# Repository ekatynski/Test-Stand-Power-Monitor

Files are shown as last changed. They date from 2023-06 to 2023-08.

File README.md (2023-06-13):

View this project on [CADLAB.io](https://cadlab.io/project/27045). 

# Test-Stand-Power-Monitor
A small board for cheaply and easily monitoring a motor test stand for a host of data types.

## Function
This board is capable of monitoring the following:
- 1x Voltage input
- 1x Hall Effect Sensor output (current measuring)
- 1x Displacement Sensor interface
- 1x UART (ESCs have UART telemetry output)
- 1x 1K RTD for temperature monitoring

In addition, this board is capable of operating a relay to control a contactor protecting the test stand power supply, as well as a CAN bus to interface with other sensory hardware in development utilizing CAN. In doing so, this board could monitor ESC power consumption, ESC temperature, ESC telemetry output, motor displacement, and eventually eRPM pending future hardware development. Prior test stand setups had used a Teensy 4.1 to monitor telemetry and perform no other function, so this board's development was to expand the amount of test stand monitoring that could be done cheaply while using a less costly and more available microcontroller in the event that it were damaged and required replacement.

## To-Do
Firmware to perform said monitoring has not yet been developed. This board utilizes an ESP32 microcontroller, chosen because it can be configured to communicate over WiFi out of the box, but I have not taken the time to write the C++ needed to make this board useful yet.

## Assembly Guide
If interested, an interactive BOM is available in this repo at `/bom/Test-Stand-Power-Monitor_2023-06-12_22-39-21.html`.

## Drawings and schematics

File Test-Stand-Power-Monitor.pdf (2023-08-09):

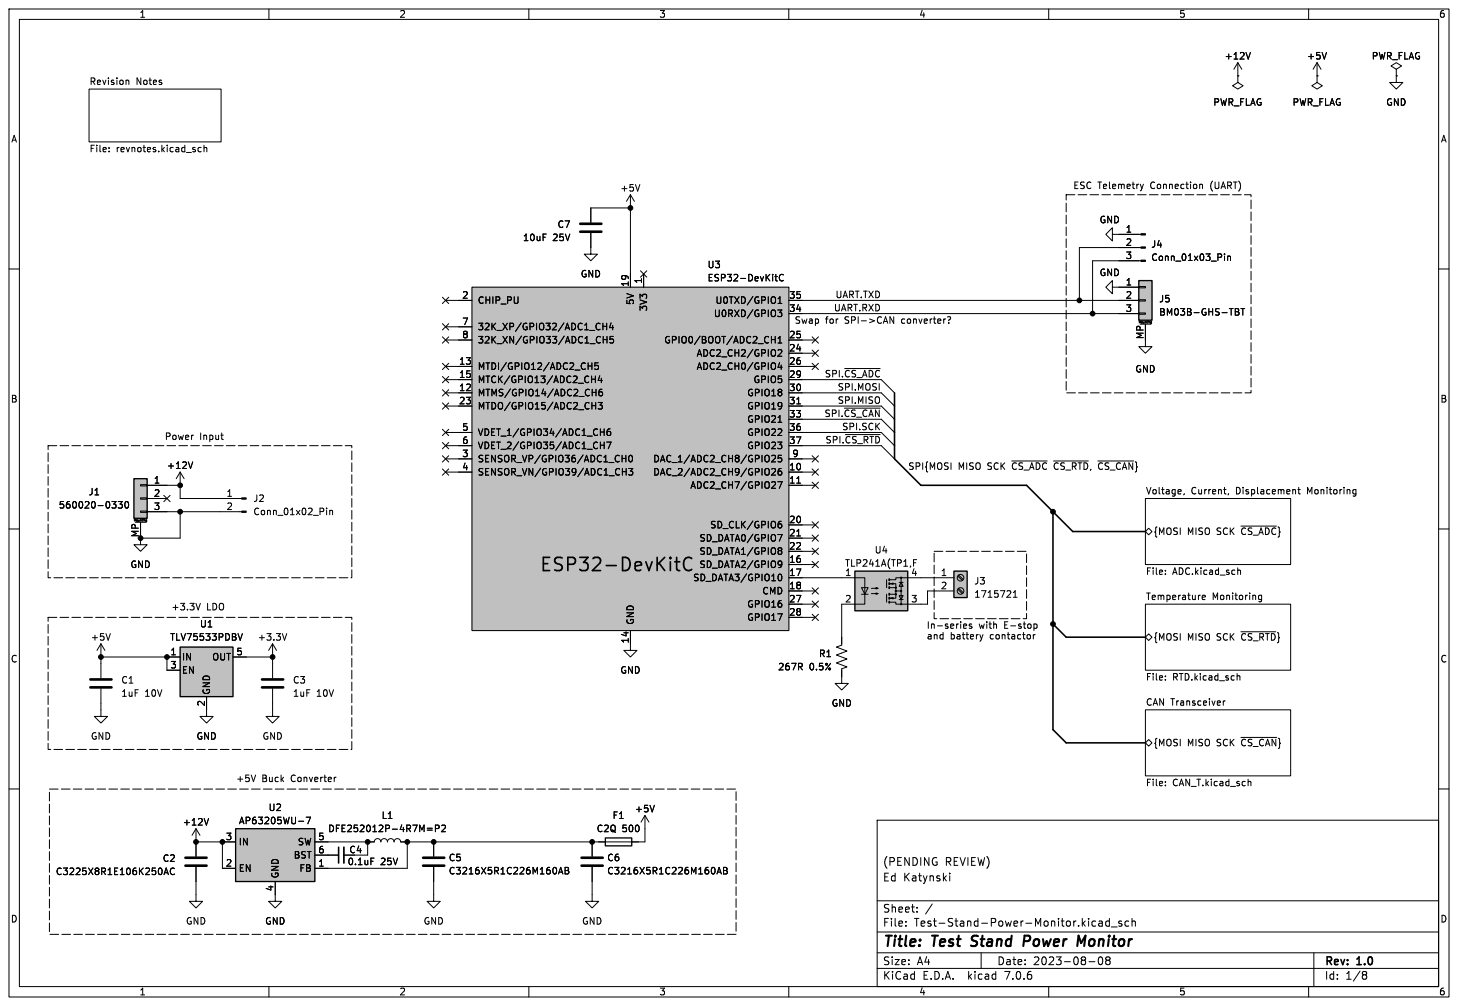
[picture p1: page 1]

Revision Notes File: revnotes.kicad_sch

1 DAC_2/ADC2_CH9/GPIO26 10 ADC2_CH7/GPIO27 11 MTMS/GPIO14/ADC2_CH6 12 MTDI/GPIO12/ADC2_CH5 13 MTCK/GPIO13/ADC2_CH4 15 SD_DATA2/GPIO9 16 SD_DATA3/GPIO10 17 CMD 18 CHIP_PU 2 SD_CLK/GPIO6 20 SD_DATA0/GPIO7 21 SD_DATA1/GPIO8 22 MTDO/GPIO15/ADC2_CH3 23 ADC2_CH2/GPIO2 24 GPIO0/BOOT/ADC2_CH1 25 ADC2_CH0/GPIO4 26 GPIO16 27 GPIO17 28 GPIO5 29 SENSOR_VP/GPIO36/ADC1_CH0 3 GPIO18 30 GPIO19 31 GPIO21 33 U0RXD/GPIO3 34 U0TXD/GPIO1 35 GPIO22 36 GPIO23 37 SENSOR_VN/GPIO39/ADC1_CH3 4 VDET_1/GPIO34/ADC1_CH6 5 VDET_2/GPIO35/ADC1_CH7 6

SPI{MOSI MISO SCK ~{CS_ADC}~{CS_RTD},~{CS_CAN}} SPI.MOSI
SPI.MISO
SPI.~{CS_CAN} SPI.SCK

{MOSI MISO SCK ~{CS_CAN}} CAN Transceiver File: CAN_T.kicad_sch

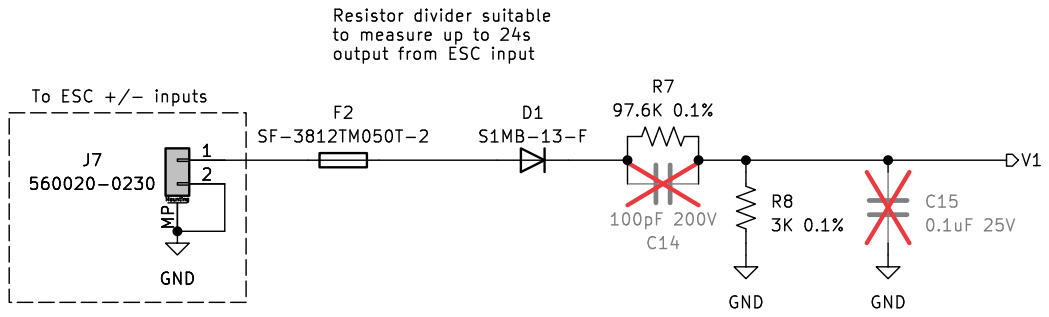
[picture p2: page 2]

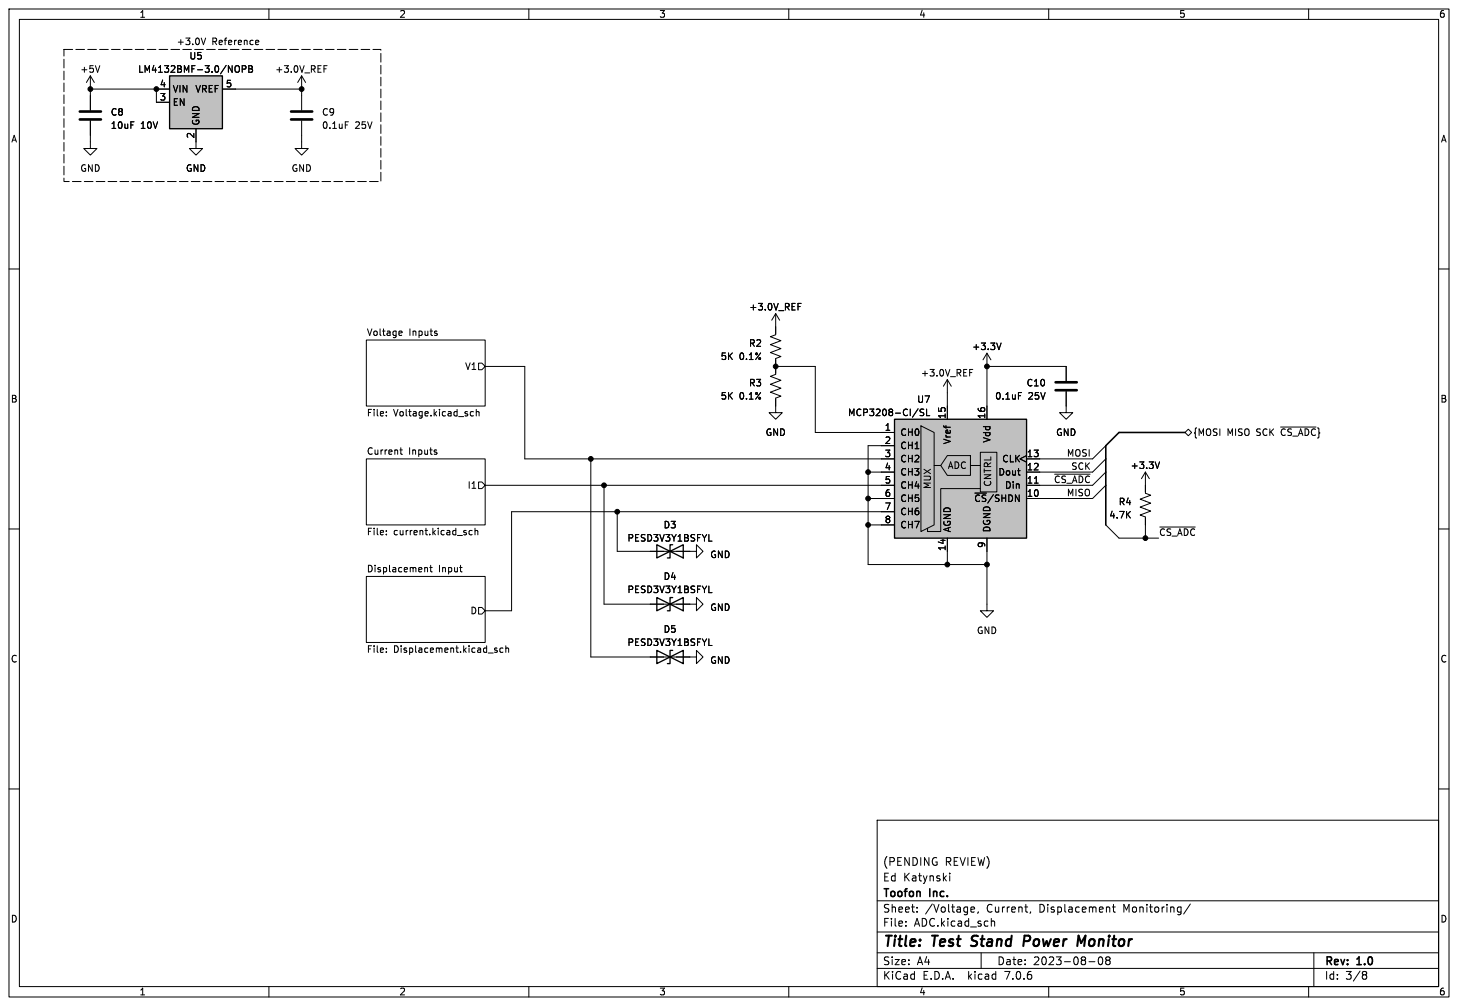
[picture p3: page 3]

V1 Voltage Inputs File: Voltage.kicad_sch D

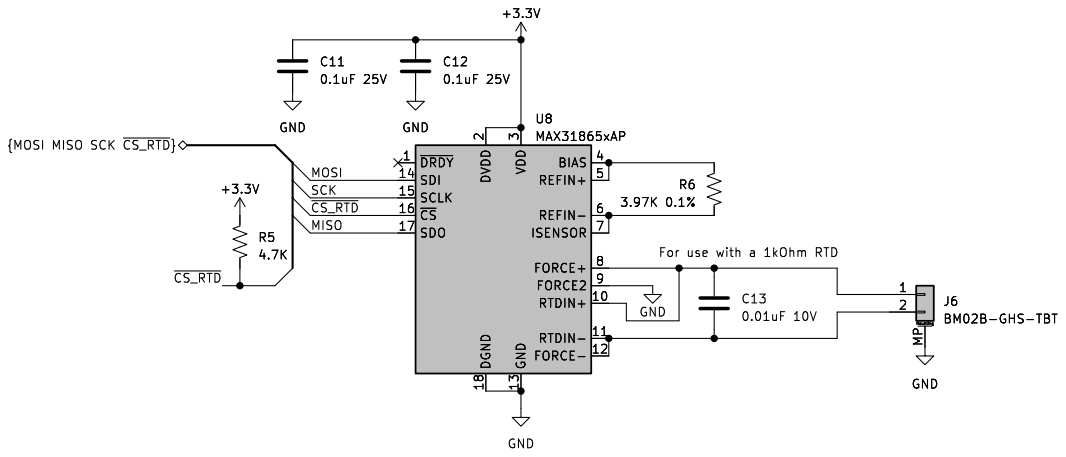
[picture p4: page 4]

J6BM02B-GHS-TBT GND GND

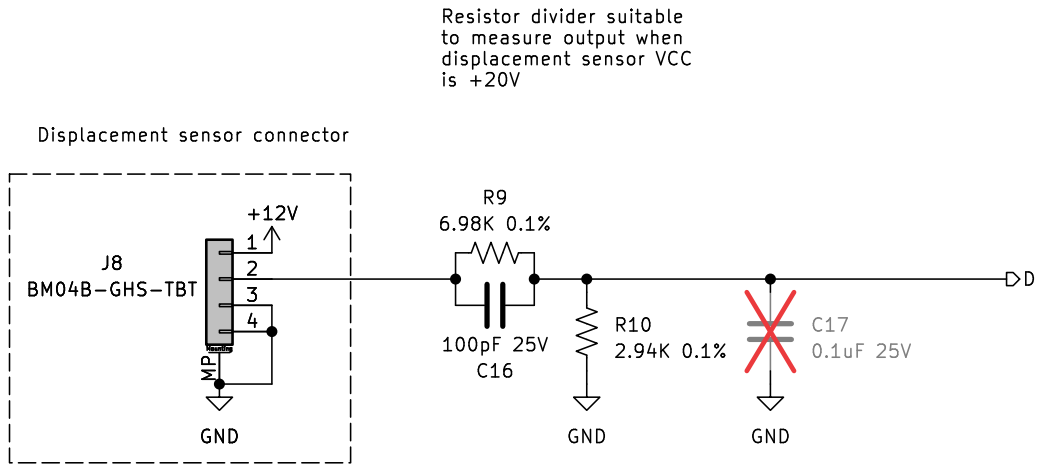
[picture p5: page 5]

to measure output when

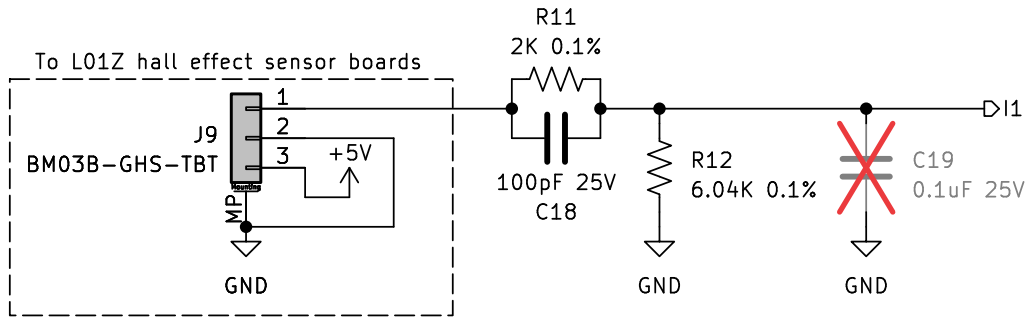
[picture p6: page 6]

I1 To L01Z hall effect sensor boards GND

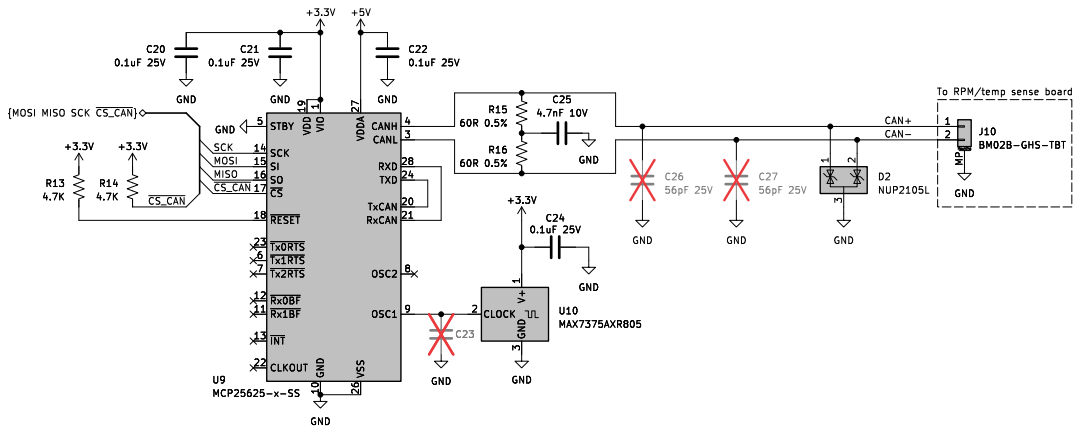
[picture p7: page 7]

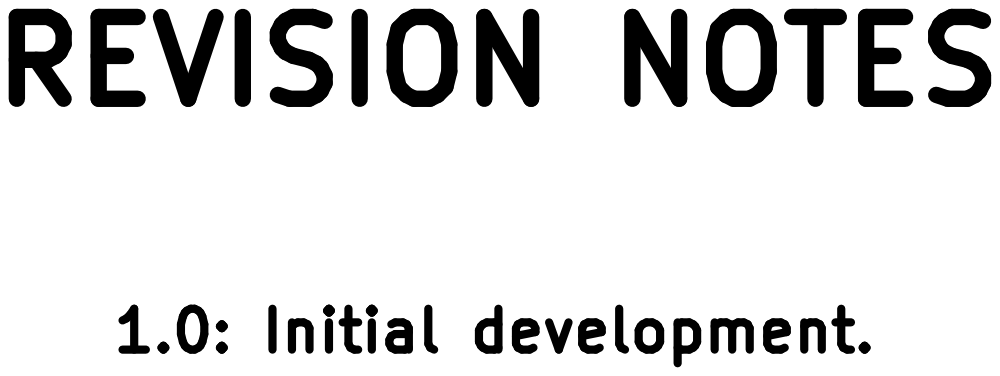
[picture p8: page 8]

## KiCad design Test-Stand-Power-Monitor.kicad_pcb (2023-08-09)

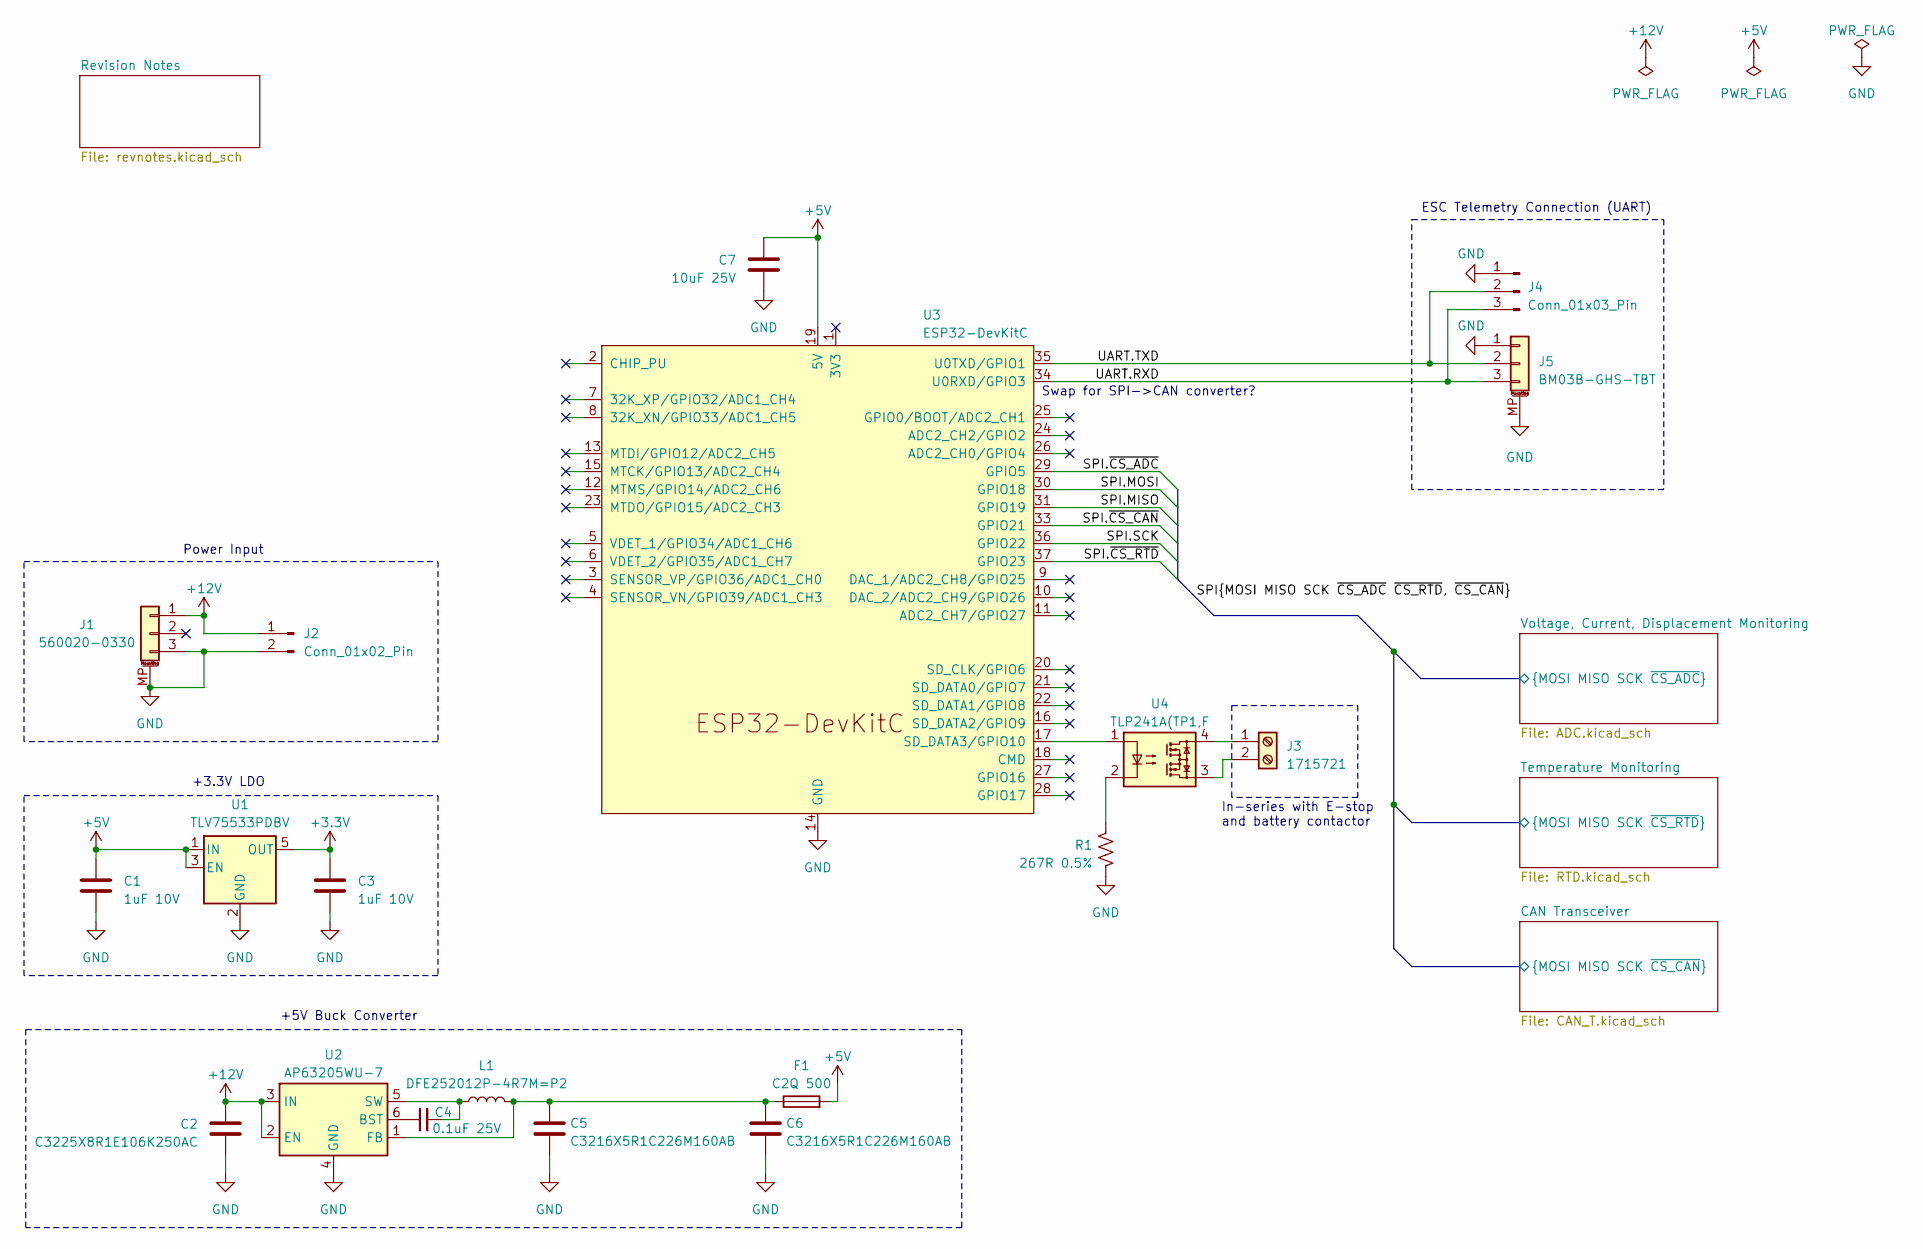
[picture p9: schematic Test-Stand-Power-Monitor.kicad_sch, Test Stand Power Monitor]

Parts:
C1, C3: 1uF 10V; C_0603_1608Metric_Pad1.08x0.95mm_HandSolder
C2: C3225X8R1E106K250AC; C_1210_3225Metric
C4: 0.1uF 25V; C_0402_1005Metric_Pad0.74x0.62mm_HandSolder
C5, C6: C3216X5R1C226M160AB; C_1206_3216Metric
C7: 10uF 25V; C_0603_1608Metric_Pad1.08x0.95mm_HandSolder
F1: C2Q 500; Fuse_0603_1608Metric
J1: 560020-0330; MOLEX_5600200330
J2: Conn_01x02_Pin; PinHeader_1x02_P2.54mm_Vertical
J3: 1715721; TerminalBlock_Phoenix_MKDS-1,5-2-5.08_1x02_P5.08mm_Horizont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
J4: Conn_01x03_Pin; PinHeader_1x03_P2.54mm_Vertical
J5: BM03B-GHS-TBT; JST_GH_BM03B-GHS-TBT_1x03-1MP_P1.25mm_Vertical
L1: DFE252012P-4R7M=P2; L_1008_2520Metric_Pad1.43x2.20mm_HandSolder
R1: 267R 0.5%; R_0402_1005Metric_Pad0.72x0.64mm_HandSolder
U1: TLV75533PDBV; SOT-23-5
U2: AP63205WU-7; TSOT-23-6
U3: ESP32-DevKitC
U4: TLP241A(TP1,F; OnSemi_CASE100CY

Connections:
+3.3V: C3.1, U1.5 (OUT); also elsewhere on the board
+5V: C1.1, C7.1, F1.2, U1.1 (IN), U1.3 (EN), U3.19 (5V); also elsewhere on the board
+12V: C2.1, J1.1, J2.1, U2.2 (EN), U2.3 (IN); also elsewhere on the board
/SPI.MISO: U3.31 (GPIO19); also elsewhere on the board
/SPI.MOSI: U3.30 (GPIO18); also elsewhere on the board
/SPI.SCK: U3.36 (GPIO22); also elsewhere on the board
/SPI.~CS_ADC: U3.29 (GPIO5); also elsewhere on the board
/SPI.~CS_CAN: U3.33 (GPIO21); also elsewhere on the board
/SPI.~CS_RTD: U3.37 (GPIO23); also elsewhere on the board
/UART.RXD: J4.3, J5.3, U3.34 (U0RXD/GPIO3)
/UART.TXD: J4.2, J5.2, U3.35 (U0TXD/GPIO1)
GND: C1.2, C2.2, C3.2, C5.2, C6.2, C7.2, J1.3, J1.MP (MountPin), J2.2, J4.1, J5.1, J5.MP (MountPin), R1.2, U1.2 (GND), U2.4 (GND), U3.14 (GND), U3.32 (GND), U3.38 (GND); also elsewhere on the board
unnamed: J3.1, U4.4
unnamed: J3.2, U4.3
unnamed: R1.1, U4.2
unnamed: C4.1, U2.6 (BST)
unnamed: C5.1, C6.1, F1.1, L1.2, U2.1 (FB)
unnamed: C4.2, L1.1, U2.5 (SW)
unnamed: U3.17 (SD_DATA3/GPIO10), U4.1

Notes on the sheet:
In-series with E-stop and battery contactor
Power Input
+3.3V LDO
ESC Telemetry Connection (UART)
+5V Buck Converter
Swap for SPI->CAN converter?

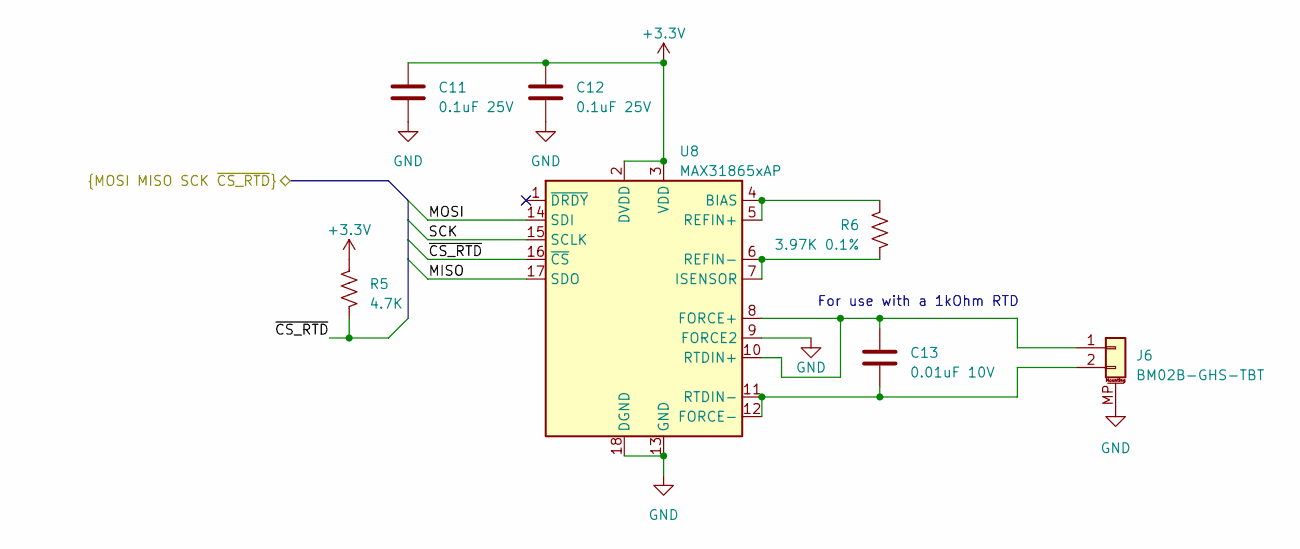
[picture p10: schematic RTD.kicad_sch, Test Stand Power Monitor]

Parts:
C11, C12: 0.1uF 25V; C_0402_1005Metric_Pad0.74x0.62mm_HandSolder
C13: 0.01uF 10V; C_0402_1005Metric_Pad0.74x0.62mm_HandSolder
J6: BM02B-GHS-TBT; JST_GH_BM02B-GHS-TBT_1x02-1MP_P1.25mm_Vertical
R5: 4.7K; R_0402_1005Metric_Pad0.72x0.64mm_HandSolder
R6: 3.97K 0.1%; R_0402_1005Metric_Pad0.72x0.64mm_HandSolder
U8: MAX31865xAP; SSOP-20_5.3x7.2mm_P0.65mm

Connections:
+3.3V: C11.1, C12.1, R5.1, U8.2 (DVDD), U8.3 (VDD); also elsewhere on the board
/SPI.MISO: U8.17 (SDO); also elsewhere on the board
/SPI.MOSI: U8.14 (SDI); also elsewhere on the board
/SPI.SCK: U8.15 (SCLK); also elsewhere on the board
/SPI.~CS_RTD: R5.2, U8.16 (~CS); also elsewhere on the board
GND: C11.2, C12.2, J6.MP (MountPin), U8.9 (FORCE2), U8.13 (GND), U8.18 (DGND), U8.19 (GND); also elsewhere on the board
unnamed: C13.1, J6.1, U8.8 (FORCE+), U8.10 (RTDIN+)
unnamed: C13.2, J6.2, U8.11 (RTDIN-), U8.12 (FORCE-)
unnamed: R6.1, U8.4 (BIAS), U8.5 (REFIN+)
unnamed: R6.2, U8.6 (REFIN-), U8.7 (ISENSOR)

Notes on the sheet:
For use with a 1kOhm RTD

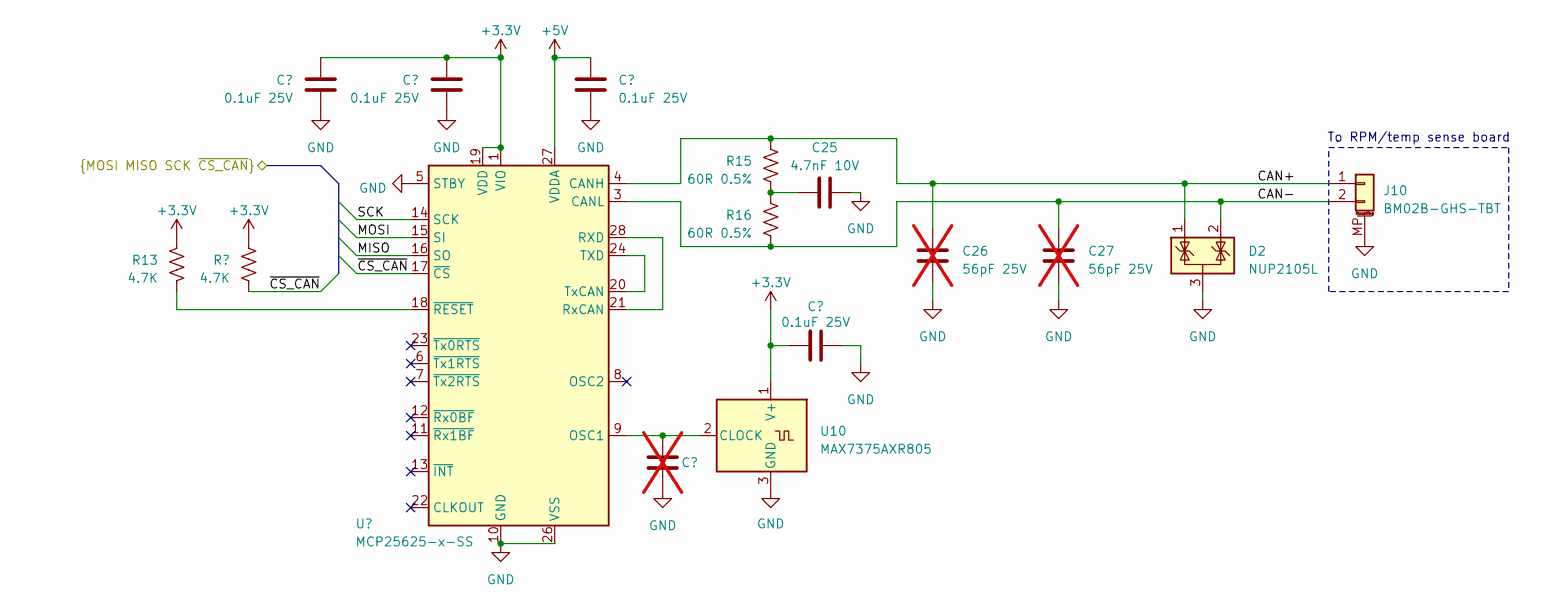
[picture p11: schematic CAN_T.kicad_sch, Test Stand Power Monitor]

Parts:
C20, C21, C22, C24: 0.1uF 25V; C_0402_1005Metric_Pad0.74x0.62mm_HandSolder
C23: C_0402_1005Metric_Pad0.74x0.62mm_HandSolder; not fitted
C25: 4.7nF 10V; C_0402_1005Metric_Pad0.74x0.62mm_HandSolder
C26, C27: 56pF 25V; C_0402_1005Metric_Pad0.74x0.62mm_HandSolder; not fitted
D2: NUP2105L; SOT-23
J10: BM02B-GHS-TBT; JST_GH_BM02B-GHS-TBT_1x02-1MP_P1.25mm_Vertical
R13, R14: 4.7K; R_0402_1005Metric_Pad0.72x0.64mm_HandSolder
R15, R16: 60R 0.5%; R_0603_1608Metric_Pad0.98x0.95mm_HandSolder
U9: MCP25625-x-SS; SSOP-28_5.3x10.2mm_P0.65mm
U10: MAX7375AXR805; SOT-323_SC-70

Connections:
+3.3V: C20.1, C21.1, C24.1, R13.1, R14.1, U9.1 (VIO), U9.19 (VDD), U10.1 (V+); also elsewhere on the board
+5V: C22.1, U9.27 (VDDA); also elsewhere on the board
/CAN Transceiver/CAN+: C26.2, D2.1 (K), J10.1, R15.1, U9.4 (CANH)
/CAN Transceiver/CAN-: C27.2, D2.2 (K), J10.2, R16.2, U9.3 (CANL)
/SPI.MISO: U9.16 (SO); also elsewhere on the board
/SPI.MOSI: U9.15 (SI); also elsewhere on the board
/SPI.SCK: U9.14 (SCK); also elsewhere on the board
/SPI.~CS_CAN: R14.2, U9.17 (~CS); also elsewhere on the board
GND: C20.2, C21.2, C22.2, C23.2, C24.2, C25.2, C26.1, C27.1, D2.3 (A), J10.MP (MountPin), U9.5 (STBY), U9.10 (GND), U9.26 (VSS), U10.3 (GND); also elsewhere on the board
unnamed: C25.1, R15.2, R16.1
unnamed: U9.21 (RxCAN), U9.28 (RXD)
unnamed: U9.20 (TxCAN), U9.24 (TXD)
unnamed: R13.2, U9.18 (~RESET)
unnamed: C23.1, U9.9 (OSC1), U10.2 (CLOCK)

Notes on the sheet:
To RPM/temp sense board

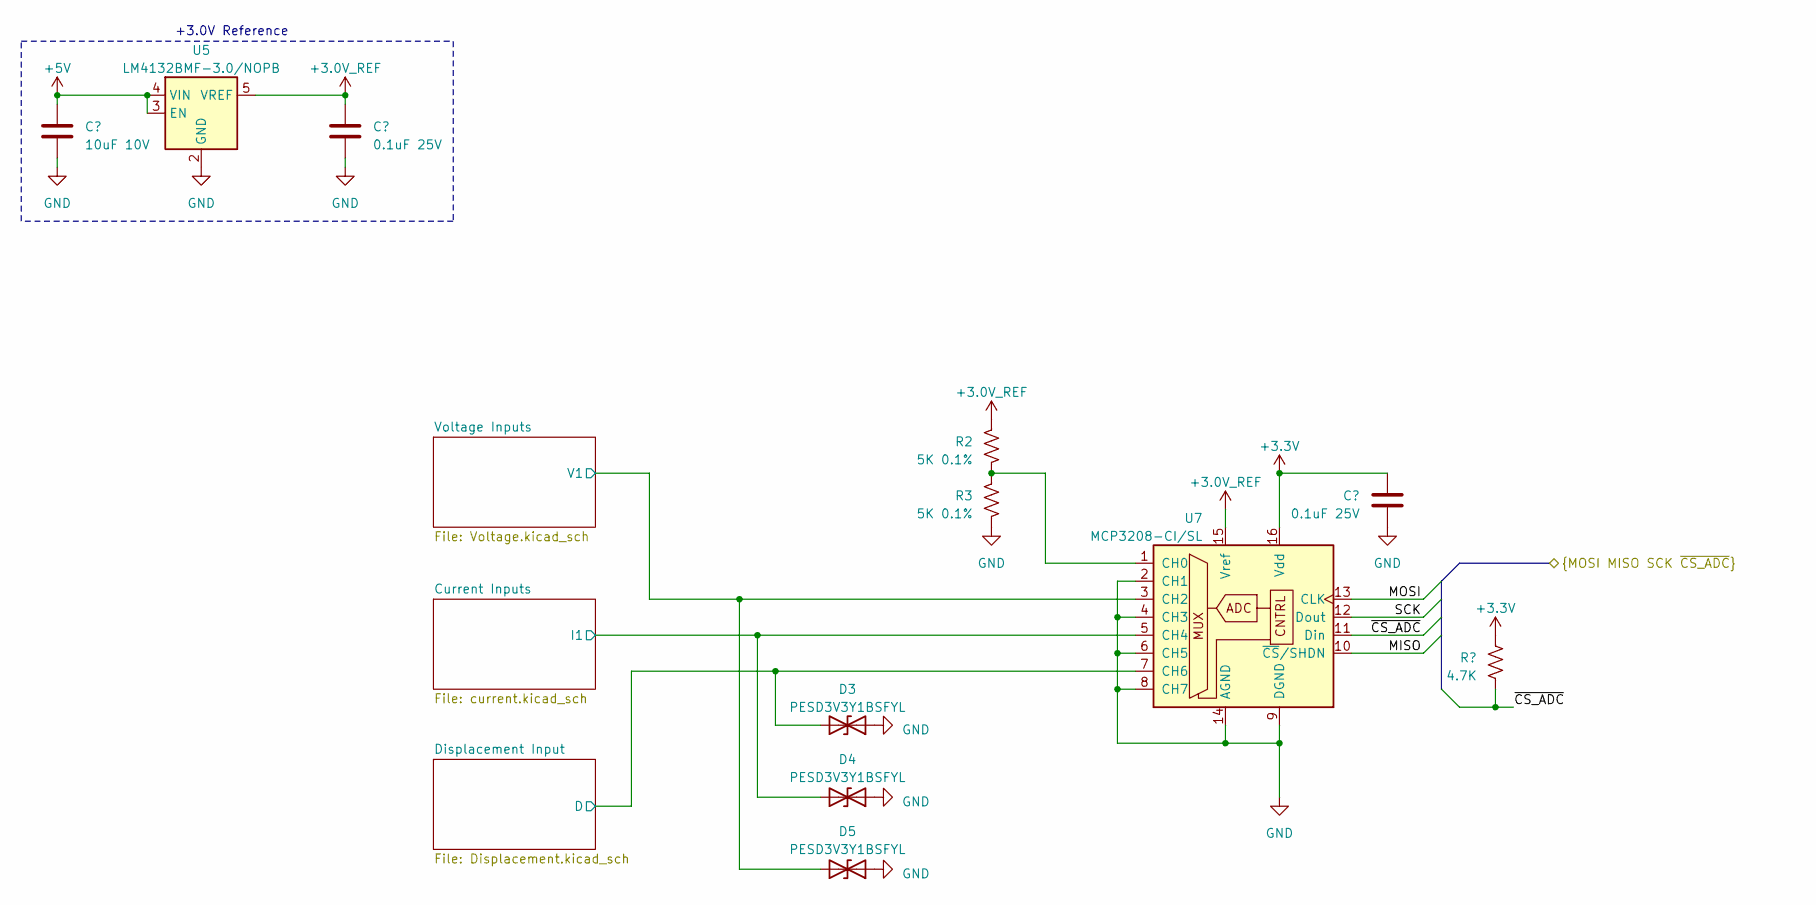
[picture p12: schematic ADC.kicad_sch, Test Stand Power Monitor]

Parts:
C8: 10uF 10V; C_0603_1608Metric_Pad1.08x0.95mm_HandSolder
C9, C10: 0.1uF 25V; C_0402_1005Metric_Pad0.74x0.62mm_HandSolder
D3, D4, D5: PESD3V3Y1BSFYL; D_0201_0603Metric
R2, R3: 5K 0.1%; R_0402_1005Metric_Pad0.72x0.64mm_HandSolder
R4: 4.7K; R_0402_1005Metric_Pad0.72x0.64mm_HandSolder
U5: LM4132BMF-3.0/NOPB; SOT-23-5
U7: MCP3208-CI/SL; SOIC-16_3.9x9.9mm_P1.27mm

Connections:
+3.0V_REF: C9.1, R2.1, U5.5 (VREF), U7.15 (Vref)
+3.3V: C10.1, R4.1, U7.16 (Vdd); also elsewhere on the board
+5V: C8.1, U5.3 (EN), U5.4 (VIN); also elsewhere on the board
/SPI.MISO: U7.10 (~CS/SHDN); also elsewhere on the board
/SPI.MOSI: U7.13 (CLK); also elsewhere on the board
/SPI.SCK: U7.12 (Dout); also elsewhere on the board
/SPI.~CS_ADC: R4.2, U7.11 (Din); also elsewhere on the board
/Voltage, Current, Displacement Monitoring/Current Inputs/I1: D4.2 (A2), U7.5 (CH4); also elsewhere on the board
/Voltage, Current, Displacement Monitoring/Displacement Input/D: D3.2 (A2), U7.7 (CH6); also elsewhere on the board
/Voltage, Current, Displacement Monitoring/Voltage Inputs/V1: D5.2 (A2), U7.3 (CH2); also elsewhere on the board
GND: C8.2, C9.2, C10.2, D3.1 (A1), D4.1 (A1), D5.1 (A1), R3.2, U5.2 (GND), U7.2 (CH1), U7.4 (CH3), U7.6 (CH5), U7.8 (CH7), U7.9 (DGND), U7.14 (AGND); also elsewhere on the board
unnamed: R2.2, R3.1, U7.1 (CH0)

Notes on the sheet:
+3.0V Reference

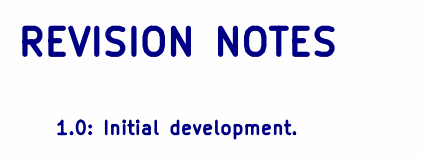
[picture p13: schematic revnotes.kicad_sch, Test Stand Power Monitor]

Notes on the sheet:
REVISION NOTES
1.0: Initial development.

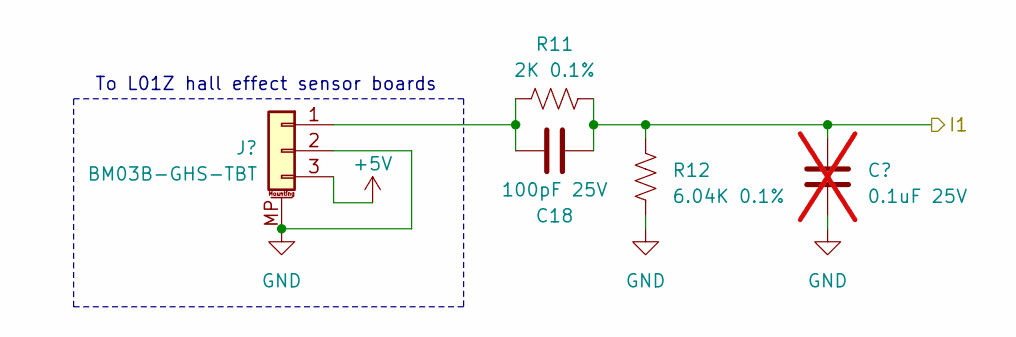
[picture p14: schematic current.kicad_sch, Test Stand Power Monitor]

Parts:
C18: 100pF 25V; C_0402_1005Metric_Pad0.74x0.62mm_HandSolder
C19: 0.1uF 25V; C_0402_1005Metric_Pad0.74x0.62mm_HandSolder; not fitted
J9: BM03B-GHS-TBT; JST_GH_BM03B-GHS-TBT_1x03-1MP_P1.25mm_Vertical
R11: 2K 0.1%; R_0402_1005Metric_Pad0.72x0.64mm_HandSolder
R12: 6.04K 0.1%; R_0402_1005Metric_Pad0.72x0.64mm_HandSolder

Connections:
+5V: J9.3; also elsewhere on the board
/Voltage, Current, Displacement Monitoring/Current Inputs/I1: C18.2, C19.1, R11.2, R12.1; also elsewhere on the board
GND: C19.2, J9.2, J9.MP (MountPin), R12.2; also elsewhere on the board
unnamed: C18.1, J9.1, R11.1

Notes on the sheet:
To L01Z hall effect sensor boards

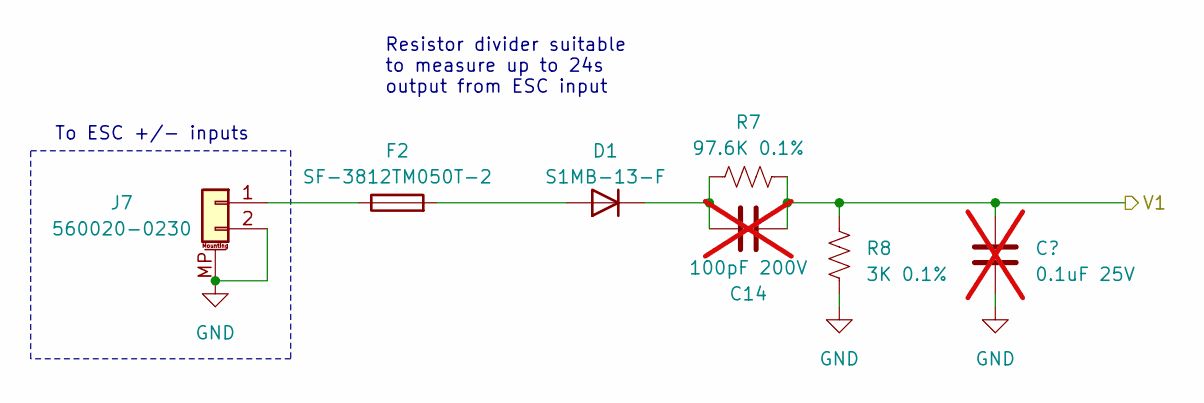
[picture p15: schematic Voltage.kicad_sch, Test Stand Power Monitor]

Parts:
C14: 100pF 200V; C_0603_1608Metric_Pad1.08x0.95mm_HandSolder; not fitted
C15: 0.1uF 25V; C_0402_1005Metric_Pad0.74x0.62mm_HandSolder; not fitted
D1: S1MB-13-F; D_SMA-SMB_Universal_Handsoldering
F2: SF-3812TM050T-2
J7: 560020-0230; MOLEX_5600200230
R7: 97.6K 0.1%; R_0805_2012Metric_Pad1.20x1.40mm_HandSolder
R8: 3K 0.1%; R_0402_1005Metric_Pad0.72x0.64mm_HandSolder

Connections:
/Voltage, Current, Displacement Monitoring/Voltage Inputs/V1: C14.2, C15.1, R7.2, R8.1; also elsewhere on the board
GND: C15.2, J7.2, J7.MP (MountPin), R8.2; also elsewhere on the board
unnamed: D1.2 (A), F2.2
unnamed: C14.1, D1.1 (K), R7.1
unnamed: F2.1, J7.1

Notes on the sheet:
Resistor divider suitable to measure up to 24s output from ESC input
To ESC +/- inputs

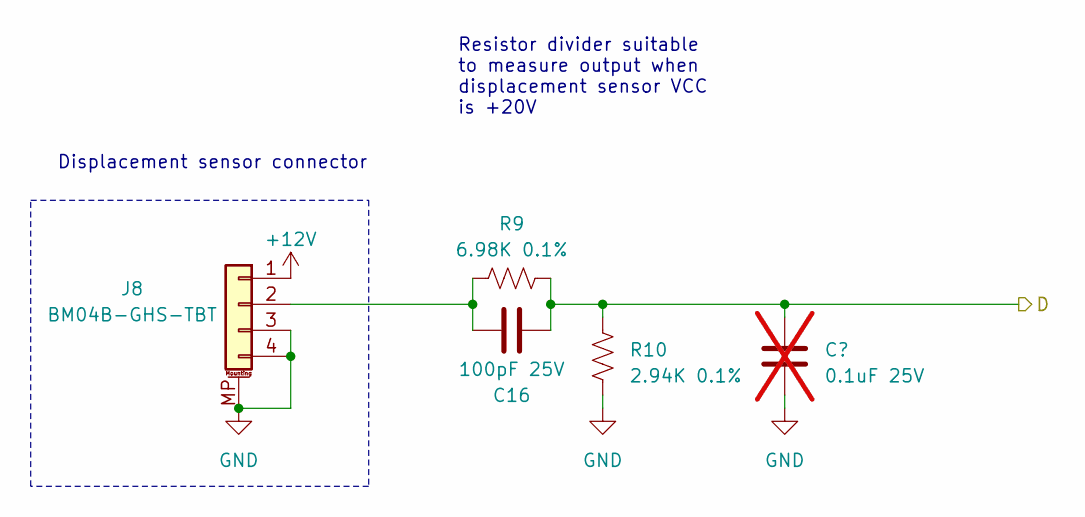
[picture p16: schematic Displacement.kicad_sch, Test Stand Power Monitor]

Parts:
C16: 100pF 25V; C_0402_1005Metric_Pad0.74x0.62mm_HandSolder
C17: 0.1uF 25V; C_0402_1005Metric_Pad0.74x0.62mm_HandSolder; not fitted
J8: BM04B-GHS-TBT; JST_GH_BM04B-GHS-TBT_1x04-1MP_P1.25mm_Vertical
R9: 6.98K 0.1%; R_0402_1005Metric_Pad0.72x0.64mm_HandSolder
R10: 2.94K 0.1%; R_0402_1005Metric_Pad0.72x0.64mm_HandSolder

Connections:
+12V: J8.1; also elsewhere on the board
/Voltage, Current, Displacement Monitoring/Displacement Input/D: C16.2, C17.1, R9.2, R10.1; also elsewhere on the board
GND: C17.2, J8.3, J8.4, J8.MP (MountPin), R10.2; also elsewhere on the board
unnamed: C16.1, J8.2, R9.1

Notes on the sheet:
Displacement sensor connector
Resistor divider suitable to measure output when displacement sensor VCC is +20V

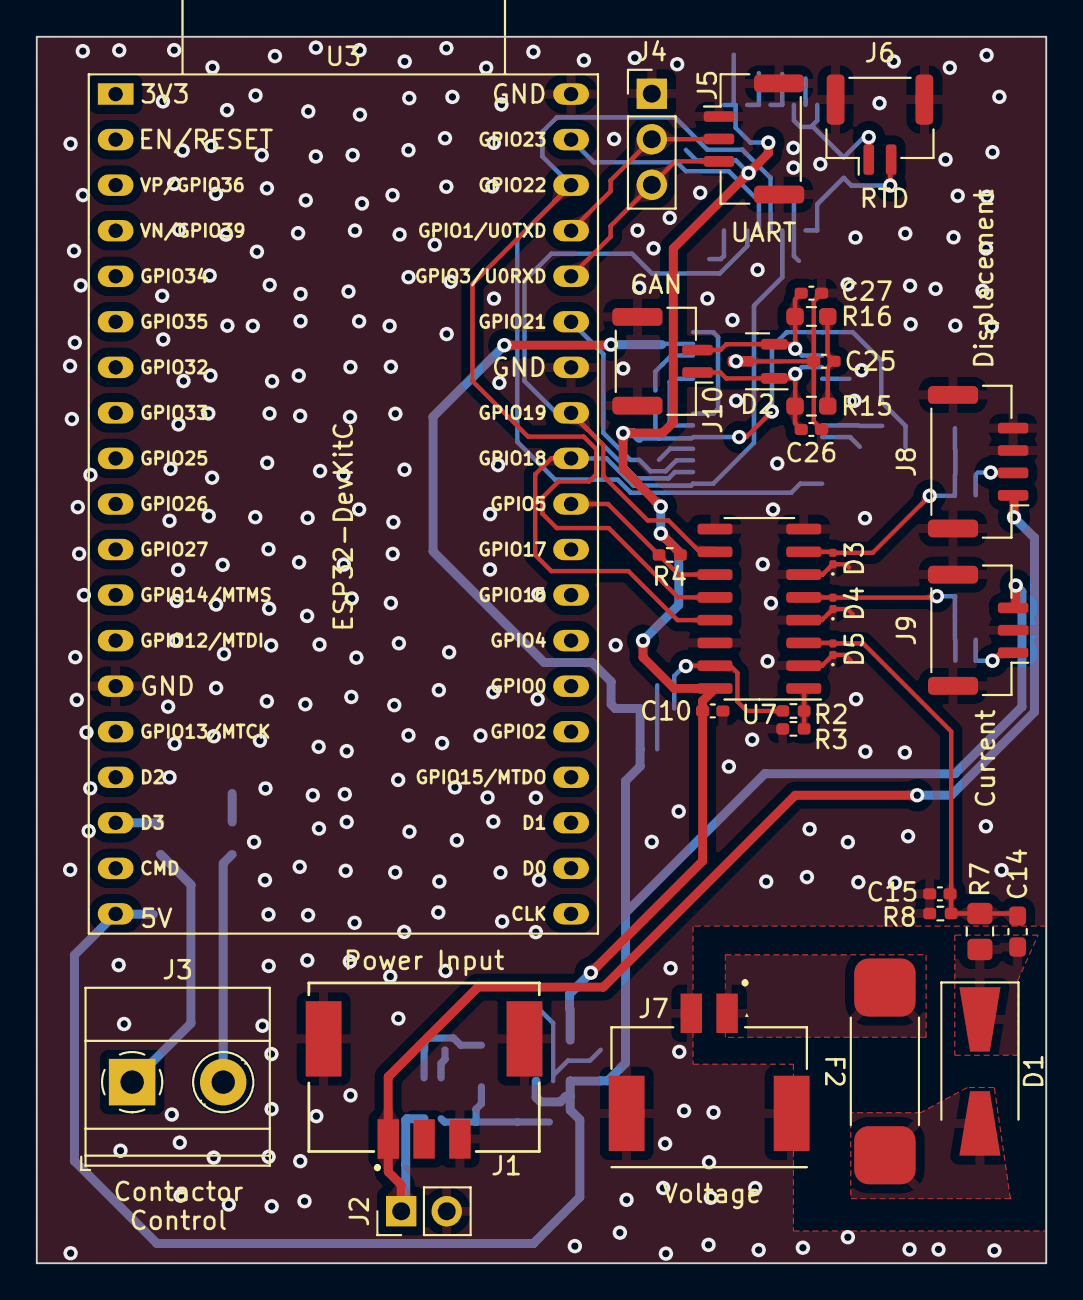
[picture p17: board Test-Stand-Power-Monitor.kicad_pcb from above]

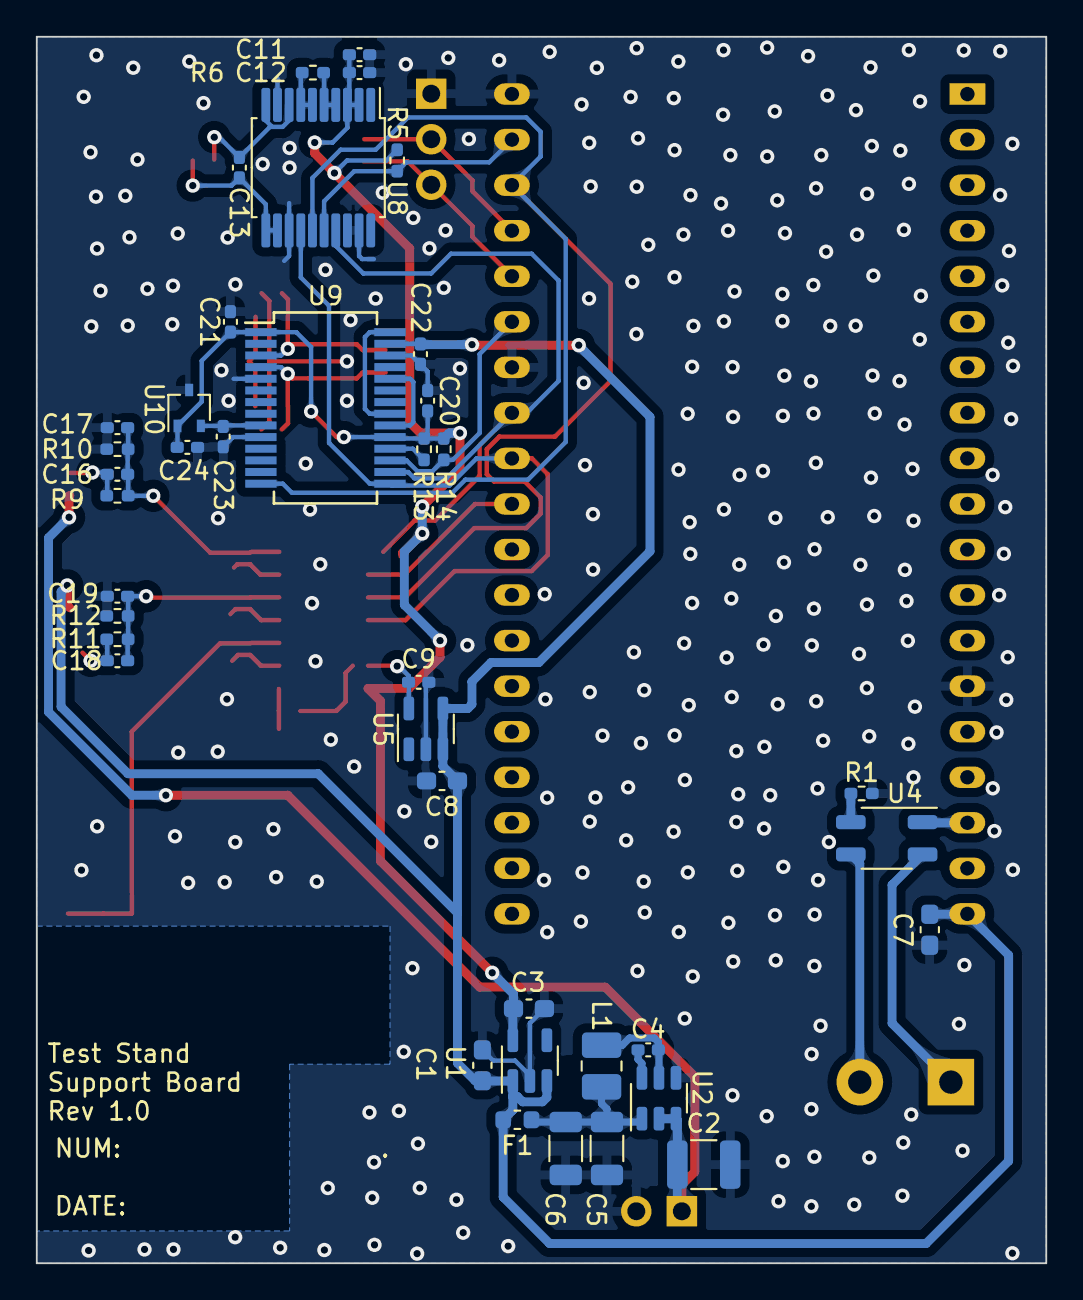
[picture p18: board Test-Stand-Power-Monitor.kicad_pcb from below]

Board: 4 copper layers, 56.3 x 68.4 mm, 70 parts (39 on the bottom side), 40 nets.

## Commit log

2023-06-13 Mass-adding all project files from prior development.
    [ADC.kicad_sch, CAN.kicad_sch, CAN_T.kicad_sch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]
2023-06-13 Generated assembly guide.
2023-06-13 Marked two-pin header as DNI to prevent short risk for +12V after testing.
    [Test-Stand-Power-Monitor.kicad_sch]
2023-06-13 Schematic re-render.
2023-08-09 Removed schematic backup files from git tracking
2023-08-09 Removed old assembly guide files
2023-08-09 Removed tracking for autosaved PCB file
2023-08-09 Removed unused schematic file.
    [CAN.kicad_sch]
2023-08-09 Imported updated files from office verison of this project
    [ADC.kicad_sch, CAN_T.kicad_sch, Displacement.kicad_sch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]
2023-08-09 Slight 3.3V power trace movement for improved ground pour
    [Test-Stand-Power-Monitor.kicad_pcb]
2023-08-09 Teardrop update
    [Test-Stand-Power-Monitor.kicad_pcb]
2023-08-09 Replotted schematic
